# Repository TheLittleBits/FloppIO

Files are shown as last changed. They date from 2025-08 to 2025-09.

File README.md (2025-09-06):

# FloppIO: The Modular Floppy Music Player 💾🎶
Modular FDD, scanner and HDD music setup for Raspberry Pi

## Description
FloppIO is a Raspberry Pi-powered floppy orchestra to use with midi files. It uses two pico microcontrollers to control 4 HDDs, 2 flatbed scanners and 8 FDDs. The Raspberry Pi computer sends commands and notes through a serial port to the Picos.

### Floppy Disk Drives
The first pico controls 8 FDDs. To output signals for multiple devices at the same time, each PIO state machine controls one FDD. A state machine is like a small CPU core that runs assembly code to control one or more gpio pins. This is a handy and unique thing in the Pico's RP2040 and RP2350 chips.
A floppy disk drive requires three signals to make music: STEP, DIR and ENABLE. The STEP signal moves the reader head one step, while DIR sets the direction. ENABLE starts the drive and turns on the small green led. The pico pulses the STEP pin at the right frequency while also setting the direction. When playing a note, the ENABLE pin is activated to turn on the led. Note: the ENABLE pin is actually called **Drive Select B**.

### Hard Disk Drives
It's nice to have some chords and melody instruments, but music without percussion is quite boring. Hard drives make a unique clicking sound when there's too much power in the actuator arm coil (which bangs to its stop). The second pico controls 4 drives with a dual H-bridge chip (see chapter Installation).

### Flatbed scanner
We need linear non-vibrating movement for high-pitched sounds. Scanners are able to do that because of the large space between the start and end of the reader head. The second pico (that also controls the HDDs) has outputs for 2 scanners. A scanner is controlled by a DRV8825, so the outputs are STEP, DIR and ENABLE. The scanner code works in a similar way as the FDD program does, but the direction is managed by another state machine. There are also two inputs (one for each scanner) that are used for endstop switches. When a signal of 3.3V is provided, the movement direction changes.

## Installation
### Setup #1
> [!WARNING]
> Bluetooth will be disabled after the setup. Save any content, because your pi reboots afterwards.
> `setup.sh` is only tested on Raspberry Pi 4. Completing the setup on older or
> newer devices is at your own risk.

<ol>
	<li>Download the latest release (on your pi) and run the `setup.sh` script in order to install FloppIO.</li>
	<li>At the following dialog, go to:</li>
	<ol type="1">
		<li>Interface Options</li>
		<li>-> Serial Port</li>
		<li>-> Enable serial login: No</li>
		<li>-> Enable serial port hardware: Yes</li>
		<li>-> Ok</li>
		<li>-> If asked for reboot, answer no</li>
		<li>-> Finish</li>
	</ol>
  <li>After some setups, a text editor appears. Look in the open file for `dtoverlay=...`. If it is, edit the value to `disable-bt`. Otherwise, manually add `dtoverlay=disable-bt` to the end of the file. Then look for `enable_uart=...`. Set the value to 1 and if `enable_uart` is not available, add `enable_uart=1` yourself. Press Ctrl-S and Ctrl-X to save and leave the editor.</li>
  <li>Your pi will reboot</li>
</ol>

### Setup #2
> [!WARNING]
> If your Raspberry Pi Pico is already flashed, any flashed content will be removed. Proceed at own risk.

Connect the first pico to your pi while pressing the on-board BOOTSEL button. If done correctly, the pico device should appear in file explorer.

Go to the floppio directory and move `floppy.elf` to your pico's mount folder. The pico will unmount itself and the code is loaded. Check if the green led is on after a second or two.

Now, disconnect the first pico and connect the second as shown above. Repeat the loading process with `scanner.elf`

Now your two picos are flashed. Connect the ground wires of both picos to the Raspberry Pi 4. Then connect GPIO 14 (from the pi) to GPIO 1 (from both picos). If done correctly, you should now have the UART TX connected to the UART RXes from the picos.

## Wiring and stuff
### Floppy Disk Drives
First of all, we need to power your floppy drives. You can buy berg connectors (the old connectors used to power FDDs) or you can manually put 12V and 5V on the "power connector" section of the image below. If you don't have a berg or a 12V and 5V power supply, you could consider using a common Molex 4-pin supply with jumper wires (they have the same wire order as berg connectors). Whatever you do, DON'T power the drives with 5V from your pi. The two picos should be powered through USB or VSYS, and there is no problem with connecting them at your pi.

FDD_input

Each FDD uses its STEP, DIR and ENABLE pin of the pico. Use transistors (the cheap 2N2222 for example) on a breadboard to control the FDD pins:

FDD

The breadboard inputs are connected to the pico using this pinout:

Pico1-pinout

Connect the breadboard outputs to the floppy drive inputs using this diagram:
FDD_input

You can use more drives if you add more transistors, wires and resistors. Each of them needs 3 of those "level shifters", so the images above only controls one drive.

### Flatbed Scanners
> [!NOTE]
> This section is optional. You may choose to only use the FDDs and ignore the scanner part without changing anything.

> [!NOTE]
> This tutorial shows how to use the scanner with DRV8825. You may choose to use A4988 instead, but this it not tested.

For using a scanner at this project, you need to disassemble it. There is little chance you can get your scanner running afterwards, so disassembling is at your own risk. You could go looking for an old scanner at secondhand shops, because new scanners are expensive and very silent. Plus, the stepper motor wires need to be visible. After finding the right scanner, locate the stepper motor wires (DRV8825 only supports motors with 4 wires) and connect them to the DRV8825 using this diagram:

Scanner

<br>
<br>

> [!NOTE]
> Now before proceeding to the pico setup, you need to trim the potentiometer according to the motors rated current. Just set up all everything as in the image above, WITHOUT the STEP and DIR pin connected. You must also leave the stepper disconnected. Power 3.3V to the SLP pin (in addition to the other 3V3 powered pins) and 12V to the bottom rail to activate the driver. Connect voltage meter to the GROUND and the little potentiometer to measure the VREF. Make sure VREF is under 0.1V, and if it doesn't work you can also increase the VREF (by turning the potentiometer). Afterwards, disconnect the SLP from the 3.3V supply, connect the stepper wires and continue.

Find a power source of 12 volts to power the breadboard's bottom power rail. The upper power rail only needs logic voltage of 3.3V (from the pico). Connect the orange wires to the pico's DRV8825-corresponding pins using this diagram:

Pico2-pinout

If you are using two scanners, use another DRV8825 with the above diagram. Only change the pico's output pins to 'DRV8825 __2__ ...' instead of 'DRV8825 __1__ ...'.

Next, use the image below to connect the two scanner endstops to the pico. Each button has to be glued or mounted on the opposite sides of the scanner. When the reader head hits a button, it changes the direction. Without endstops, your scanner won't do that and hit the edge. Be careful and test multiple times if this part is set up correctly.

Endstops

Your scanners should now be up and running.

### Hard Disk Drives
> [!NOTE]
> This section is optional. You may choose to only use the FDDs and ignore the HDD part without changing anything.

Connecting hard drives to the FloppIO network is more complicated than adding scanners or floppy drives. You need to solder the HDD coil ends to a wire yourself, which destroys the drive and all the data on it. Proceed at your own risk.

Locate the drive's coil ends and test them with a 3.3V power source. If the coil reader arm moves, you are fine. If it moves but not with a _snap_ sound, apply more voltage. Use the image below to connect the wires you just found to the breadboard:

HDD

The L293D is a dual H-bridge IC, which does a perfect job for this setup. Power the top rail with pico's logic voltage (3.3V) and the bottom rail with the voltage for your drives. One L293D chip controls 2 HDDs, so you need two of them for 4 drives. The orange wires go to the HDD-corresponding pins of the second pico (see image at chapter Scanner).

To play a song, turn on all power supplies and check your connections. If the pico's onboard leds are on, the picos are functioning.
Now you can run `python3 player.py YOURMIDIFILE` on your pi. Don't forget the `midi/` directory with working midi examples!

## Features
Current features include:
 - Pitchbend: Unlike simple note-on events, pitchwheel messages can add a special pitch-bending effect to the song. Because of the high baud rate, there is no problem sending that large amount of frequencies to the picos.
 - Power-saving mode: All pico's outputs will turn off when the 'shutdown' signal is received. The first pico stops putting signals on the STEP and DIR pins, so they actually freeze. The other pico releases tension on the HDDs and freezes output of the scanner.
 - Reset at startup: If message the `0, 0` is received on the pico, the floppy disk drives reset to their middle position.
 - Modular and easily expandable: The devices are connected in a star topology, so it's easy to add one more device. Just changing the `run_action()` function does the job.

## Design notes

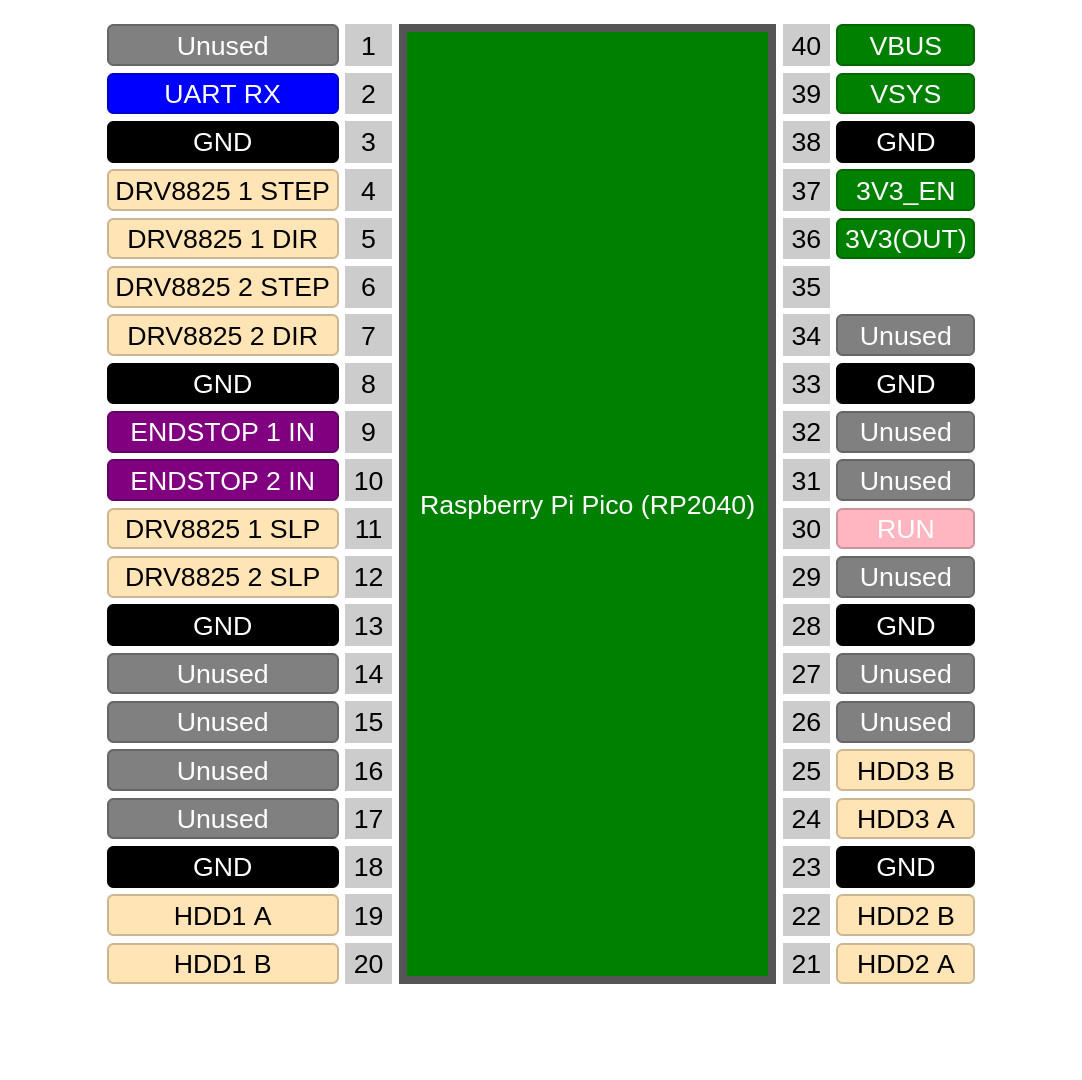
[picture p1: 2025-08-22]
Circuits/Pico2-pinout.png

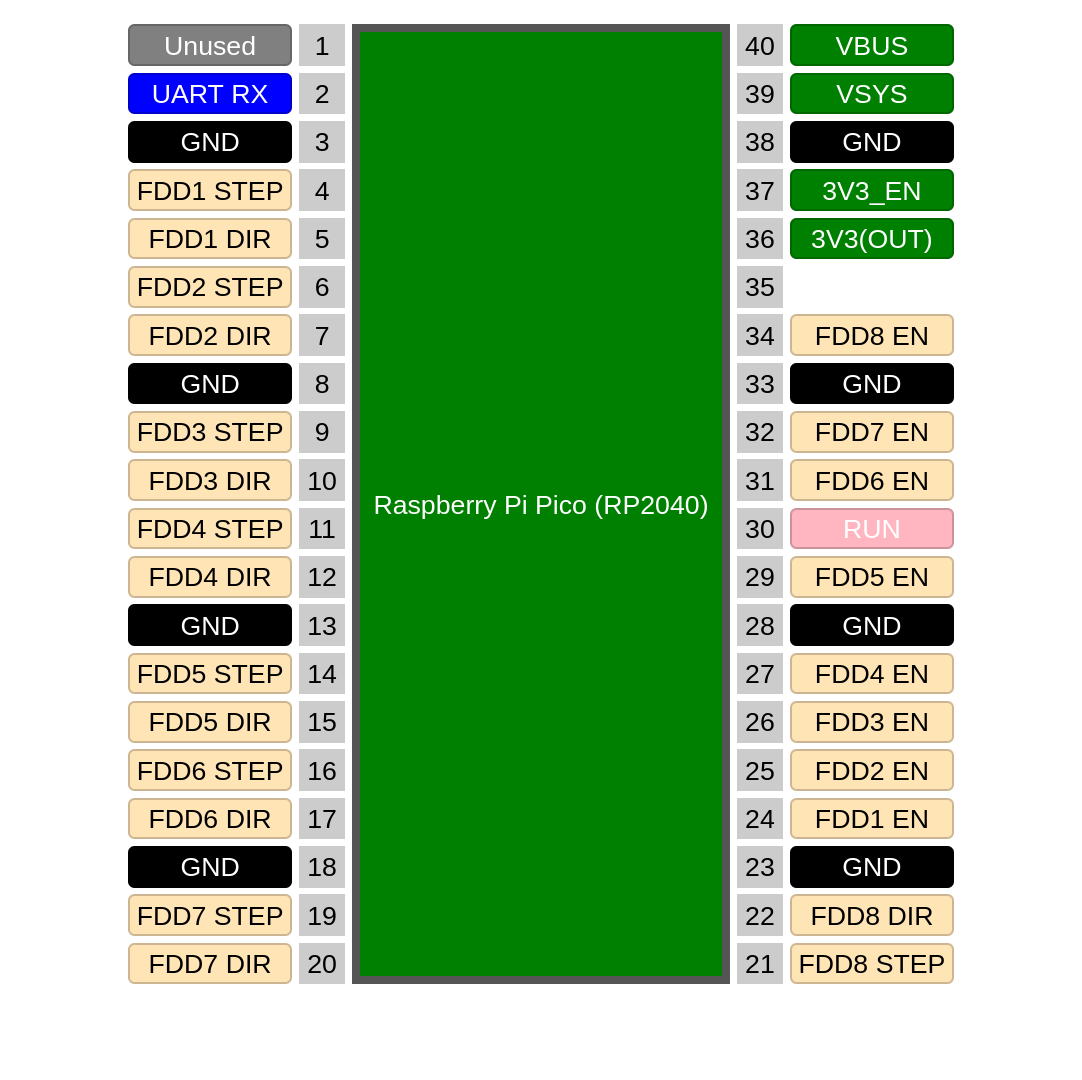
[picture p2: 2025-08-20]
Circuits/Pico1-pinout.png

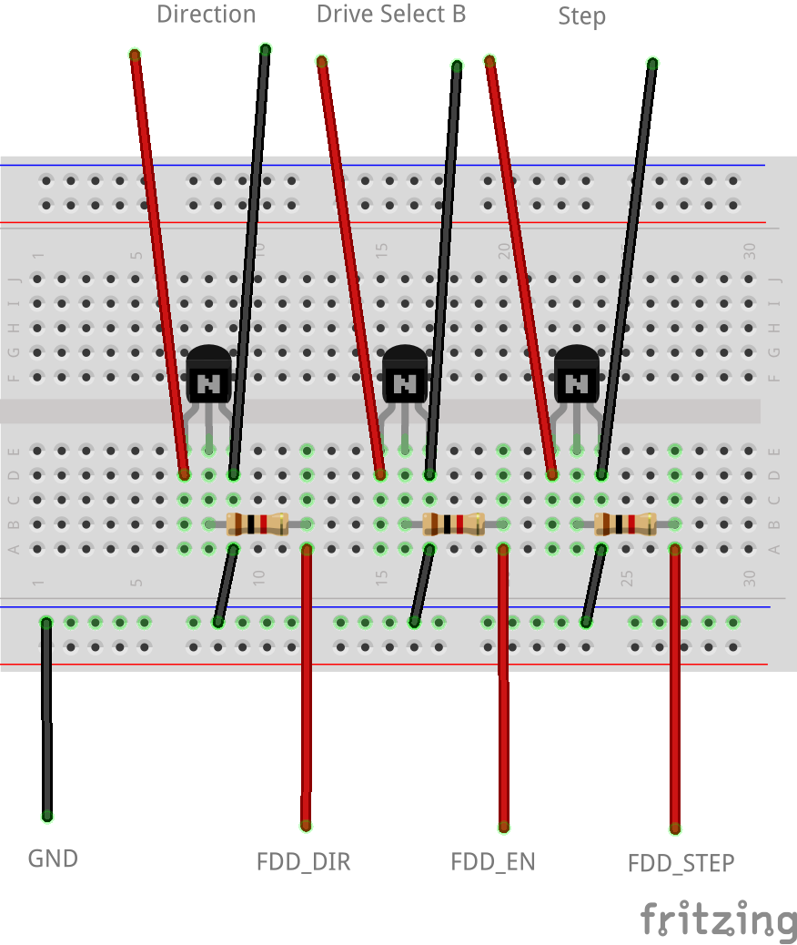
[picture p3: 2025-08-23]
Circuits/FDD.png

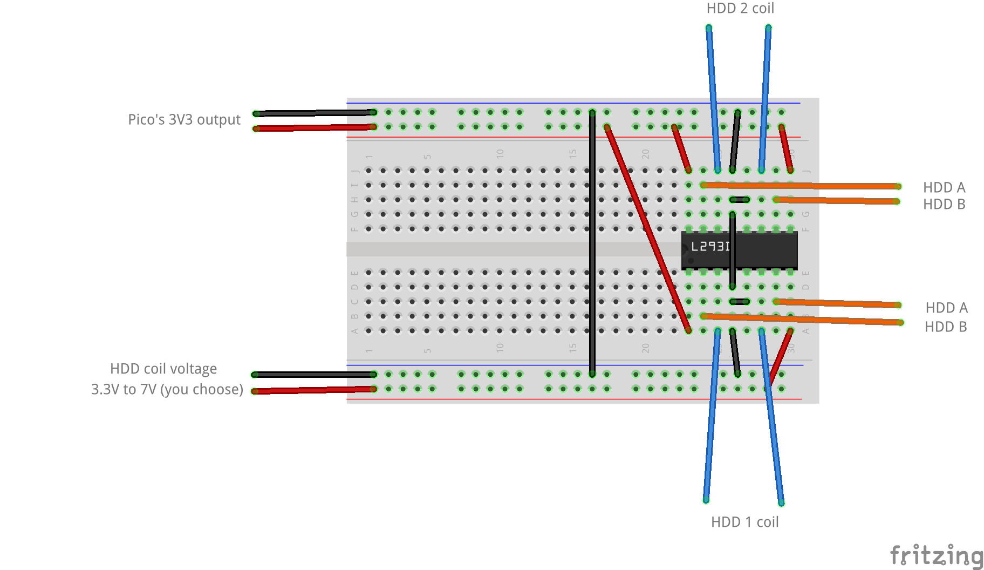
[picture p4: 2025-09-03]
Circuits/HDD.png

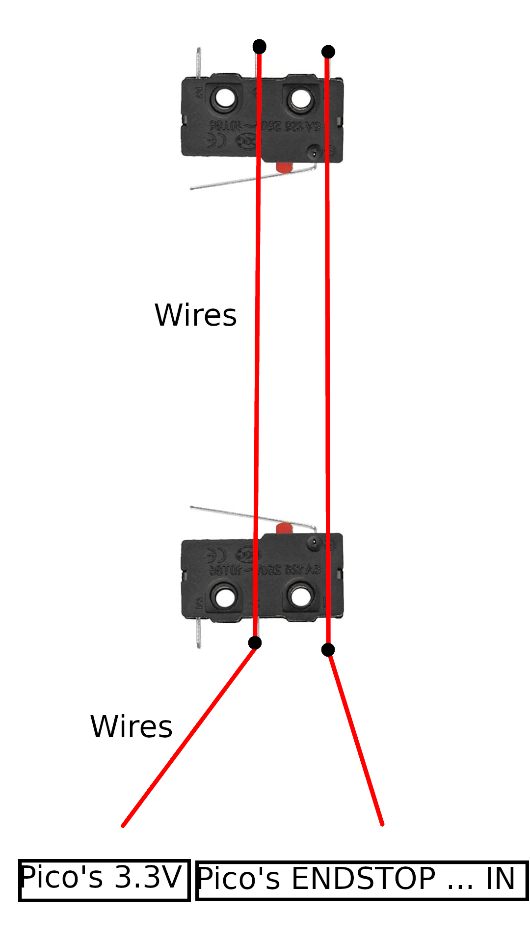
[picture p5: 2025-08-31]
Circuits/Endstops.png

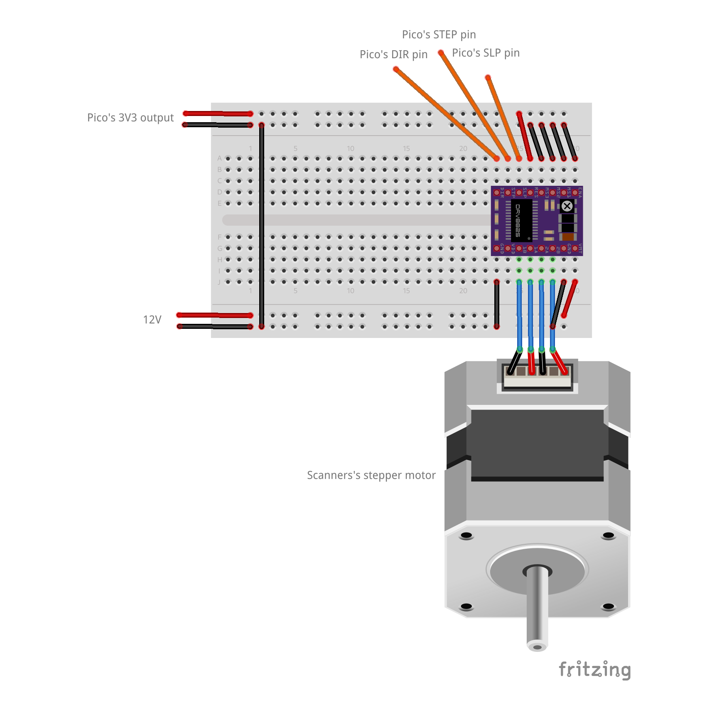
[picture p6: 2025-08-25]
Circuits/Scanner.png

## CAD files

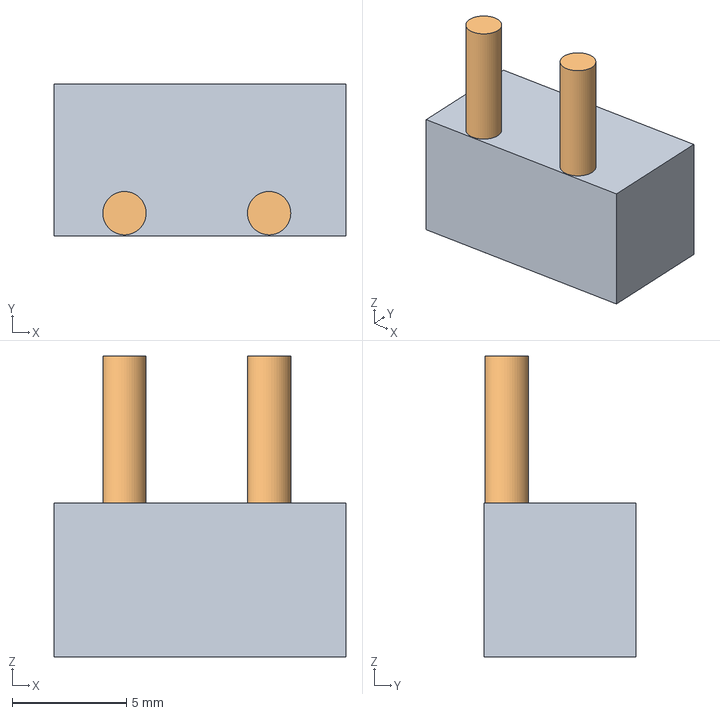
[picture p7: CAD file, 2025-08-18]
3D/Endstop-blocks.FCStd
12.8 x 6.66 x 13.2 mm

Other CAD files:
3D/Endstop-blocks.stl

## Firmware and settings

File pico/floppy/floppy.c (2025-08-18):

#include <stdio.h>
#include "pico/stdlib.h"
#include "hardware/pio.h"
#include "hardware/gpio.h"
#include "hardware/uart.h"
#include "program.pio.h"
#include "hardware/clocks.h"

#define BAUD_RATE 1000000

void init_uart() {
    // Init UART
    uart_init(uart0, BAUD_RATE);
    gpio_set_function(1, GPIO_FUNC_UART);
}

void fdd_program_init(PIO pio, uint sm, uint pin) {
    // Init one fdd program
    uint offset = pio_add_program(pio, &fdd_program);
    pio_gpio_init(pio, pin);
    pio_gpio_init(pio, pin + 1);
    pio_sm_set_consecutive_pindirs(pio, sm, pin, 2, true);
    pio_sm_config config = fdd_program_get_default_config(offset);
    sm_config_set_set_pins(&config, pin, 2);
    float div = (float)clock_get_hz(clk_sys) / 1e6f; // The clock speed has to be 1 MHz for frequency calculations
    sm_config_set_clkdiv(&config, div);
    pio_sm_init(pio, sm, offset, &config);
}

void init_pio() {
    // Init the PIO programs so they can enabled later
    fdd_program_init(pio0, 0, 2);
    fdd_program_init(pio0, 1, 4);
    fdd_program_init(pio0, 2, 6);
    fdd_program_init(pio0, 3, 8);
    fdd_program_init(pio1, 0, 10);
    fdd_program_init(pio1, 1, 12);
    fdd_program_init(pio1, 2, 14);
    fdd_program_init(pio1, 3, 16);
}

void enable_pio(bool value) {
    /* If 'value' is true, all the PIOs will be enabled. This
    function's purpose is to save processing power. */

    if (value == true) {
        pio_sm_set_enabled(pio0, 0, 1);
        pio_sm_set_enabled(pio0, 1, 1);
        pio_sm_set_enabled(pio0, 2, 1);
        pio_sm_set_enabled(pio0, 3, 1);
        pio_sm_set_enabled(pio1, 0, 1);
        pio_sm_set_enabled(pio1, 1, 1);
        pio_sm_set_enabled(pio1, 2, 1);
        pio_sm_set_enabled(pio1, 3, 1);
    } else if (value == false) {
        pio_sm_set_enabled(pio0, 0, 0);
        pio_sm_set_enabled(pio0, 1, 0);
        pio_sm_set_enabled(pio0, 2, 0);
        pio_sm_set_enabled(pio0, 3, 0);
        pio_sm_set_enabled(pio1, 0, 0);
        pio_sm_set_enabled(pio1, 1, 0);
        pio_sm_set_enabled(pio1, 2, 0);
        pio_sm_set_enabled(pio1, 3, 0);
    }
}

void init_sio() {
    // Init all ENABLE pins of the FDDs
    gpio_init(18); gpio_set_dir(18, true);
    gpio_init(19); gpio_set_dir(19, true);
    gpio_init(20); gpio_set_dir(20, true);
    gpio_init(21); gpio_set_dir(21, true);
    gpio_init(22); gpio_set_dir(22, true);
    gpio_init(26); gpio_set_dir(26, true);
    gpio_init(27); gpio_set_dir(27, true);
    gpio_init(28); gpio_set_dir(28, true);
    // Init and turn on the onboard led
    gpio_init(25); gpio_set_dir(25, true);
    gpio_put(25, 1);
}

void stop_playing(int index) {
    // Turn off the according FDD
    switch (index) {
        case 0: gpio_put(18, 0); break;
        case 1: gpio_put(19, 0); break;
        case 2: gpio_put(20, 0); break;
        case 3: gpio_put(21, 0); break;
        case 4: gpio_put(22, 0); break;
        case 5: gpio_put(26, 0); break;
        case 6: gpio_put(27, 0); break;
        case 7: gpio_put(28, 0); break;
    }
}

void start_playing(int index) {
    // Turn on the according FDD
    switch (index) {
        case 0: gpio_put(18, 1); break;
        case 1: gpio_put(19, 1); break;
        case 2: gpio_put(20, 1); break;
        case 3: gpio_put(21, 1); break;
        case 4: gpio_put(22, 1); break;
        case 5: gpio_put(26, 1); break;
        case 6: gpio_put(27, 1); break;
        case 7: gpio_put(28, 1); break;
    }
}

void set_frequency(int index, int freq) {
    /* Load the delay value into the according TX FIFO.
    The PIO delay code part has a "SET" instruction and a
    "JMP" instruction, so one delay loop cycle takes
    two microsecond. That's why the delay value is split in
    half. */

    switch (index) {
        case 0: pio_sm_put_blocking(pio0, 0, 1000000/freq/2); break;
        case 1: pio_sm_put_blocking(pio0, 1, 1000000/freq/2); break;
        case 2: pio_sm_put_blocking(pio0, 2, 1000000/freq/2); break;
        case 3: pio_sm_put_blocking(pio0, 3, 1000000/freq/2); break;
        case 4: pio_sm_put_blocking(pio1, 0, 1000000/freq/2); break;
        case 5: pio_sm_put_blocking(pio1, 1, 1000000/freq/2); break;
        case 6: pio_sm_put_blocking(pio1, 2, 1000000/freq/2); break;
        case 7: pio_sm_put_blocking(pio1, 3, 1000000/freq/2); break;
    }
}

int reset() {
    #define DIRECTION_MASK 174760    // Binary: 0b00000000000101010101010101000
    #define STEP_MASK      87380     // Binary: 0b00000000000010101010101010100
    #define LED_MASK       477888512 // Binary: 0b11100011111000000000000000000
    #define ALL_MASK       478150652 // Binary: 0b11100011111111111111111111100

    // Init all used pins
    gpio_init_mask(ALL_MASK);
    gpio_set_dir_out_masked(ALL_MASK);

    // Activate all FDDs
    gpio_set_mask(LED_MASK);

    // Move the head to max position
    gpio_clr_mask(DIRECTION_MASK);

    for (int i = 0; i < 85; i++) {
        gpio_set_mask(STEP_MASK);
        sleep_ms(10);
        gpio_clr_mask(STEP_MASK);
        sleep_ms(10);
    }

    // Change direction and move to the centre
    gpio_set_mask(DIRECTION_MASK);

    for (int i = 0; i < 42; i++) {
        gpio_set_mask(STEP_MASK);
        sleep_ms(10);
        gpio_clr_mask(STEP_MASK);
        sleep_ms(10);
    }

    gpio_clr_mask(ALL_MASK);
    gpio_init_mask(ALL_MASK); // "Deinit" all the used pins
}

void run_action(uint action, uint value) {
    /* Each pico has it's own action table. Here are the
    8 FDDs starting at 12. 0 - 9 are reserved for
    parameters and auxiliary actions */

    switch (action) {
        case 0: reset(); init_pio(); init_sio(); break;
        case 1: enable_pio(value); break;
        case 2: break;
        case 3: break;
        case 4: break;
        case 5: break;
        case 6: break;
        case 7: break;
        case 8: break;
        case 9: break;
        case 10: break; // Scanner #1
        case 11: break; // Scanner #2
        case 12: if (value == 0) {stop_playing(action - 12);} else {set_frequency(action - 12, value); start_playing(action - 12);} break;
        case 13: if (value == 0) {stop_playing(action - 12);} else {set_frequency(action - 12, value); start_playing(action - 12);} break;
        case 14: if (value == 0) {stop_playing(action - 12);} else {set_frequency(action - 12, value); start_playing(action - 12);} break;
        case 15: if (value == 0) {stop_playing(action - 12);} else {set_frequency(action - 12, value); start_playing(action - 12);} break;
        case 16: if (value == 0) {stop_playing(action - 12);} else {set_frequency(action - 12, value); start_playing(action - 12);} break;
        case 17: if (value == 0) {stop_playing(action - 12);} else {set_frequency(action - 12, value); start_playing(action - 12);} break;
        case 18: if (value == 0) {stop_playing(action - 12);} else {set_frequency(action - 12, value); start_playing(action - 12);} break;
        case 19: if (value == 0) {stop_playing(action - 12);} else {set_frequency(action - 12, value); start_playing(action - 12);} break;
    }
}

int main() {

    // Call all startup functions
    stdio_usb_init(); // Only because the ability of updating software without entering BOOTSEL mode manually
    reset();
    init_uart();
    init_pio();
    init_sio();
    
    uint8_t action; // Here is the action stored
    uint8_t value1; // Here is the first data byte stored
    uint8_t value2; // Here the second

    for (;;) {
        action = uart_getc(uart0);
        if (action >= 128) { // Check if "action" is really an action byte and has MSB 1
            action -= 128;
            value1 = uart_getc(uart0);
            if (value1 <= 127) { // Then check if value1 is a data byte and has MSB 0
                value2 = uart_getc(uart0);
                if (value2 <= 127) { // Value2 also has to be a data byte
                    run_action(action, value1*127+value2);  // Run the action received on UART
                }
            }
        }
    }
}

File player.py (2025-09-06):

#  ______ _                  _____ ____  
# |  ____| |                |_   _/ __ \ 
# | |__  | | ___  _ __  _ __  | || |  | |
# |  __| | |/ _ \| '_ \| '_ \ | || |  | |
# | |    | | (_) | |_) | |_) || || |__| |
# |_|    |_|\___/| .__/| .__/_____\____/ 
#                | |   | |               
#                |_|   |_|               
#
#           Made by Cosmin Pirciu
#
#
# FDD, HDD and scanner music using MIDI Files

print('Loading modules...', end='')
import mido
import sys
import driver
from time import sleep
from MidiEdit import arrange_channels, arrange_drums
print('DONE')

print('''
  ______ _                  _____ ____  
 |  ____| |                |_   _/ __ \\ 
 | |__  | | ___  _ __  _ __  | || |  | |
 |  __| | |/ _ \\| '_ \\| '_ \\ | || |  | |
 | |    | | (_) | |_) | |_) || || |__| |
 |_|    |_|\\___/| .__/| .__/_____\\____/ 
                | |   | |               
                |_|   |_|               
      ''')

ENABLE_EDIT_CHANNELS = False # Whether arrange the midi channels

# Load the midi file with Mido
try:
    # Use MidiEdit to get ready the midifile for FloppIO
    if ENABLE_EDIT_CHANNELS:
        MidiFile = arrange_channels(arrange_drums(mido.MidiFile(sys.argv[1])))
    else:
        MidiFile = arrange_drums(mido.MidiFile(sys.argv[1]))

except IndexError:
    print('Please specify the midi file.')
    exit()
except OSError:
    print('Invalid file format. Probably not a midi file.')
    exit()

print('Initialising...', end = '')
driver.init() # Init the driver
print('DONE')

print('Resetting...', end = '')
driver.reset() # Init the driver
print('DONE')

print('Starting up...', end = '')
driver.startup() # Enable the FDDs and HDDs
sleep(1)
print('DONE')

def handle_msg(msg):
    if msg.type == 'pitchwheel':
        driver.pitchwheel(msg.channel, msg.pitch) # Set pitchbend for a specific channel
    if msg.type == 'note_on':
        if msg.channel == 9:
            driver.hdd(msg.note, msg.velocity) # Click the HDD
        else:
            driver.play(msg.channel, msg.note, msg.velocity) # Play a note with the fdd
    if msg.type == 'note_off':
        driver.play(msg.channel, msg.note, 0) # Stop playing a note with the fdd

def main():
    for msg in MidiFile.play():
        handle_msg(msg) # Sends the message to the message handler
    
    print('\nDone playing file. Goodbye')
    driver.cleanup() # Disables the gpio pins
    exit()


if __name__ == "__main__":
    try:
        main()
    except KeyboardInterrupt: # In case of keyboard interruption
        print("\nInterrupted by user. Closing up.")
        driver.cleanup() # Disables the gpio pins
        exit()
    except Exception as error: # In case of other errors
        print("\nAn error occured: {}.\nClosing up.".format(error))
        driver.cleanup() # Disables the gpio pins
        exit()

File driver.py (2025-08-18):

import serial as _serial
from math import floor as _floor
from math import log as _log
from time import sleep as _sleep

def _note_to_hz(note):
    # Translate a midi note to hertz
    return 440 * 2 ** ((note - 69) / 12)

def _hz_to_note(hz):
    # Translate hertz to midi notes
    if hz > 0:
        return 12 * (_log(hz/220)/_log(2)) + 57
    elif hz == 0:
        return 0
    else:
        hz *= -1
        return -1 * (12 * (_log(hz/220)/_log(2)) + 57)

def _pitch_to_note(pitch):
    # Translate the midi pitchbend value to midi note value
    return pitch / 4096

def _send(action, value):
    # Send one message over UART
    global port
    value = _floor(value)
    port.write(bytes([action + 128])) # Send the action
    port.write(bytes([_floor(value/127)])) # Send value1
    port.write(bytes([value%127])) # Send value2


def init():
    global port, db
    db = []
    # Open the serial UART port to the pico
    port = _serial.Serial('/dev/serial0', 1000000)
    # Resolve a UART bug on the pico side. Action 2 does
    # nothing, but after a reboot of pico the code skips
    # the first uart message.
    _send(2, 0)
    # Create a database with info about the 16 midi channels
    for i in range(16):
        db.append({"frequency": 0, "frequency_raw": 0, "pitchwheel": 0, "playing": False})

def startup():
    _send(1, 1) # Enable the FDDs and the HDDs

def play(channel, note, velocity):
    if velocity > 0:
        db[channel]["frequency"] = _note_to_hz(note + _pitch_to_note(db[channel]["pitchwheel"])) # Total frequency (midi note frequency + pitchbend)
        db[channel]["frequency_raw"] = _note_to_hz(note) # Only the midi note frequency
        db[channel]["playing"] = True # Whether it it playing or not
        _send(channel + 10, db[channel]["frequency"]) # Send the the channel + 10 (because channel 0 is action 10 in the pico code)
    else:
        if _note_to_hz(note) == db[channel]["frequency_raw"]: # Check if this is the note that should be turned off
            db[channel]["frequency"] = 0 # Frequency is 0, so note is not played
            db[channel]["frequency_raw"] = 0 # Same here
            db[channel]["playing"] = False # Not playing
            _send(channel + 10, 0) # Send the floppy ID plus the "off" value

def hdd(note, velocity):
    if velocity > 0:
        _send(126, note) # Action 126 is a click with the HDD

def pitchwheel(channel, pitch):
    db[channel]["pitchwheel"] = pitch # Set the pitchwheel value
    db[channel]["frequency"] = _note_to_hz(_pitch_to_note(db[channel]["pitchwheel"]) + _hz_to_note(db[channel]["frequency_raw"])) # Recalculate the frequency
    if db[channel]["playing"]: # Without this statement the floppy would play at every pitchwheel message
        _send(channel + 10, db[channel]["frequency"]) # Send the new frequency

def reset():
    _send(0, 0) # Send the reset message
    _sleep(3) # Wait for the floppies to reset

def cleanup():
    # Cleaning up
    global port
    for i in range(10, 20): # Send frequency 0 to all devices to stop playing
        _send(i, 0)
        _sleep(0.01)
    _send(1, 0) # Disable the HDDs
    port.close()

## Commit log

2025-08-19 No drum track error resolved
    [MidiEdit.py]
2025-08-22 Pico scanner outputs now freeze at power off
2025-08-22 Added breadboard image
    [FDD.fzz]
2025-08-23 Changed image
    [FDD.fzz]
2025-08-25 Added DRV8825 tutorial
    [Scanner.fzz]
2025-08-31 Endstop image for documentation
2025-09-03 Added hdd breadboard layout
    [HDD.fzz]
